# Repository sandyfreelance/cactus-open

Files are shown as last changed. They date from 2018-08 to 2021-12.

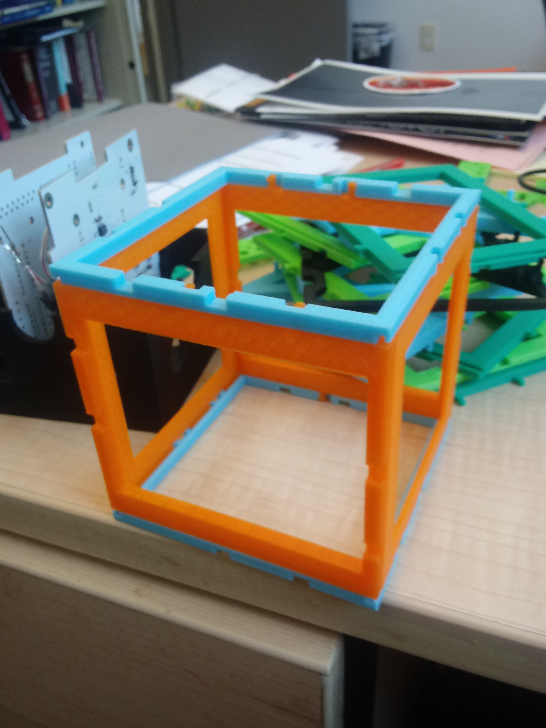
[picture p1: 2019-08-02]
PuzzleSat/PuzzleSat_Pic.jpg

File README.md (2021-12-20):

# cactus-open
Open source documentation, hardware and code for a CubeSat


We provide 4 documents for use by other CubeSat teams, 3 of which comprise our "CubeSat Cookbook".

1) CubeSat_Cookbook_Vol_1_Engineering_Guide.pdf (by R. Pierce Smith) is a comprehensive guide to building your own CubeSat at a detailed engineering level, and includes lessons learned from our Cactus-1 mission.

2) CubeSat_Cookbook_Vol_2_Newcomers_Guide.pdf (by Jorge Rodriguez) is designed for newcomers to CubeSats and discusses some of the overarcing concepts including power, mission readiness reviews, and building effective teams.

3) CubeSat_Cookbook_Vol_3_Common_EPS.pdf (by Erik Schroen) walks you through how to design and customize the electrical power system for your specific CubeSat mission (based on lessons learned from Cactus-1).

4) TheHABHandbook.pdf (by Ian Hastings) is a guide for teams starting up High Altitude Balloon projects.  Under Capitol's "Crawl, Walk, Run" philosophy, we highly recommend teams look at flying payloads and components via HAB as an effective way to iteratively improve your designs.

Acknowledgements: The Cactus-1 mission is Capitol Technology University's first CubeSat mission. Our launch opportunity was provided via the NASA CubeSat Launch Initiative. The Cactus-1 mission is supported by grants from the Maryland Space Grant Consortium (MDSGC).

5) We also provide Ralph Stormer III's "PuzzleSat" 3D-printable CubeSat structure models.  This is a simple modular system for building CubeSat-spec PC104-size-compliant test frames for 1U, 2U, 3U, and other variants so engineering teams can practice working within the CubeSat size requirements.  Documetation, STL and CAD files, and a photo are provided.  They are also fun for prototyping, and we use them for student payload low altitude tests as well.

6) We also provide our hardware schematics, CAD files, and anxillary data to help jumpstart other teams.  Our hardware on this github repository is released under the CERN Open Hardware License version 1.2.  Credit for the Work should be given to R.P. Smith in terms of authorship.  Individual items will indicate citation/credits as well.  Generally, you can use this to build your own CubeSat, the full license terms are below.

* Cactus-1 contains the files for our specific architecture
* CADD Files contains the Cactus-1 stack and board designs used
* EaglePCBs contains PC104, solar, and other bus panels suitable for modding

***********************************************************************

Specific citations and history are given for each component as follows:

Cactus-1 proposals and mission overviews: A. Antunes, R. Schrenk, R. P. Smith, A. Walters, R. Maharaja, M. Horvath

Hermes payload (on Cactus only-- for Hermes sounding rockets, see Maharaja) by C. Murray, E. Schroen (power Board design), Carlos Del Cid, R. Maharaja, P. Smith, IP rights retained by R. Maharaja

Trapsat payload by R. Schrenk, K. Moore, Z. Richards, M. Strittmatter, A. Walters, R. P. Smith, IP rights retained by R. Schrenk

3U++ Tabbed Frame: by R. P. Smith, R. Schrenk, provided under an open hardware license

Pi-CPU/Health & Safety Boards: by R. P. Smith, A. Antunes, provided under an open hardware license

Power bus: by R. P. Smith, G. Auvray, C. Odigwe, A. Antunes, R. Schrenk

Solar: (Added this because power and solar have different aspects (i.e. licensing to use) by R. P. Smith with assembly help from George Gieomekis, Marcus Bailey, Sam Lawson, Nick Keller, Sarah Sharpe, Alex English, Nick Aniello, Chris Finch

Passive Magnetics: by E. Routhier, B Reese , R. P. Smith with help by Ian Hastings, Christina Williams

Flight software by A. Antunes with help by Randy Powell, Zalika Dixon, and thanks to Alan Cudmore for useful discussion on his “PiSat” concept

Thermal blankets by R. Schrenk with help by Sarah Sharpe, Marcus Bailey, and George Giakoumakis

Comms: by M. Horvath, A. Johnson, A. Antunes

Burn wire, foot switches, inhibits, ports, and subsystems not mentioned: considered either part of the above, part of the general Cactus mission, or not sufficiently novel to merit publication or separate enumeration.

Ground team: Mark Horvath, Charis Houston, Devon Marshall, Seth Dickerson

Full list of high-level support (addendum): Alex Antunes, Angela Walters, Rishabh Maharaja, Marcel Mabsen, Patrick Stakem, Alan Cudmore, Dave McComas, Suzanne Strege, Alison Evans, Cinnamon Wright

Full list of students (addendum): Pierce Smith, Ryan Shrenk, Nathan Weideman, Mark Horvath, Alec Johnson, Chris Murray, Sarah Sharpe, George Giakoumakis, Marcus Bailey, Xavier Guzman, Marissa Jagernath, Chukwuma Odigwe, Keegan Moore, Zack Richard, Jamil Ahmed, Gary Visser, Joshua Joseph, Eric Ruthier, Sean Mullin, Christina Williams, Nick Aiello, Randy Powell, Mikus Bormanis, Christel Gesterling, Zalika Dixon, Mike Stritmatter, Josh Hernendez, Ralph Stormer III, Dan Whiteside, Bryce Reese, Charis Houston, Devon Marshall, Seth Dickerson, and others.

uploaded July 2019, updated Dec 2020

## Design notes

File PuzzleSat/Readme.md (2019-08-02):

PuzzleSat
By: Ralph A Stormer III

This work (both document and 3D printable CAD files) are licensed under a Creative Commons Attribution-NonCommercial-ShareAlike 4.0 International License. (https://creativecommons.org/licenses/by-nc-sa/4.0/).  Authorship is Ralph A. Stormer III.

PuzzleSat is a 3d printable modular CubeSat shell and internal structure system. With this system, one can build CubeSat of varying forms and configurations, including 1U CubeSats, 3U × 3U × 3U CubeSats, and miscellaneous formations like rings, spheres, and cacti (a U refers to a standard CubeSat unit which is a decimeter cube (Walker, 2017)).  As of the 7th iteration of the design, the system consists of 13 parts that interlock together to form a shell.  All parts are based off plates that interlock to form the structural support for the PC/104 Printed Circuit Board (PCB) standard. This system is meant for engineering modeling of CubeSats, as to give developers an idea of how the final product would be wired and effectively look.

Common

The common parts are the parts that one would be printed out for every CubeSat size.

Skeletal Female

The skeletal female part is one of the main structural components of PuzzleSat.  It holds the slots for a slide part as well as the openings for the snap fits of the male parts.  The term skeletal refers to there being a bracing structure in between the outer rim of this panel.  This part's secondary purpose is to act as a wall to the outside of the CubeSat.

Skeletal Male

The skeletal male part is one of the main structural components of PuzzleSat.  It holds the slots for a slide part as well as houses the snap fits that integrate with the openings of the female parts.  The term skeletal refers to there being a bracing structure in between the outer rim of this panel.  This part's secondary purpose is to act as a wall to the outside of the CubeSat.

Skeletal Slide

The skeletal slide part is a thin slide that integrates with both male and female parts.  This part allows for the PC/104 board to fit inside of the CubeSat without interfering with the other structural components.  The term skeletal refers to there being a bracing structure in between the outer edge of this panel.  This part's secondary purpose is to act as a wall to the outside of the CubeSat.

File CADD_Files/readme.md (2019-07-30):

Reference files and parts list for our PC104 boards.

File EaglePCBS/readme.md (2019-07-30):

Here are our Cactus-1 solar and bus panels in Eagle CAD format.
Other missions are free to use or repurpose these.readme.md

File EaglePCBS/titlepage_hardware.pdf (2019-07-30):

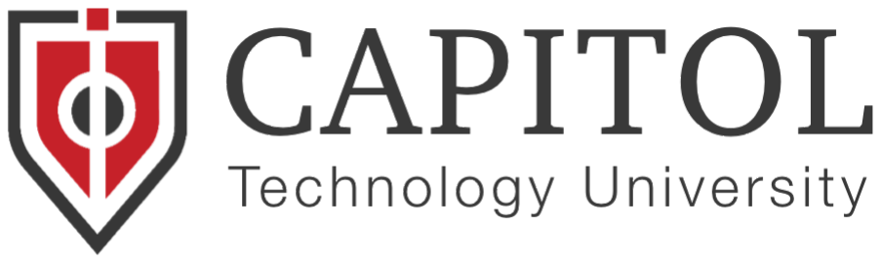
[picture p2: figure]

We provide these documents to support the CubeSat community.

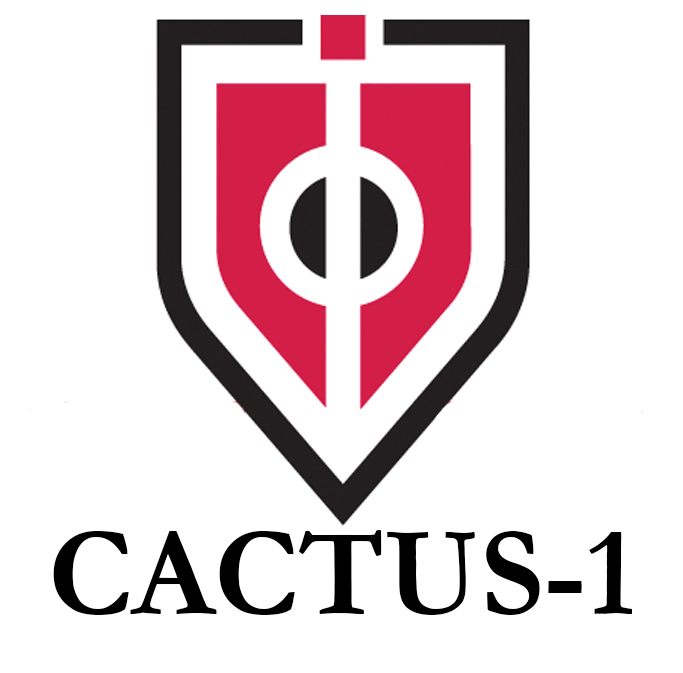
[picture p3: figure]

Acknowledgements: The Cactus-1 mission is Capitol Technology University's first CubeSat mission. Our launch opportunity was provided via the NASA CubeSat Launch Initiative. The Cactus-1 mission is supported by grants from the Maryland Space Grant Consortium (MDSGC).

All hardware is released under the CERN Open Hardware License version 1.2. Credit for the Work should be given to R.P. Smith in terms of authorship. Individual items will indicate citation/credits as well. Generally, you can use this to build your own CubeSat, the full license terms are in the included license file for CERN Open Hardware Licence v1.2.

Specific citations and history are given for each component as follows:
Cactus-1 proposals and mission overviews
A. Antunes, R. Schrenk, R. P. Smith, A. Walters, R. Maharaja, M. Horvath
Hermes payload (on Cactus only-- for Hermes sounding rockets, see Maharaja) by C. Murray, E. Schroen (power Board design), Carlos Del Cid, R. Maharaja, P. Smith, IP rights retained by R. Maharaja
Trapsat payload by R. Schrenk, K. Moore, Z. Richards, M. Strittmatter, A. Walters, R. P. Smith, IP rights retained by R. Schrenk
3U++ Tabbed Frame: by R. P. Smith, R. Schrenk, provided under an open hardware license
Pi-CPU/Health & Safety Boards: by R. P. Smith, A. Antunes, provided under an open hardware license
Power bus: by R. P. Smith, G. Auvray, C. Odigwe, A. Antunes, R. Schrenk
Solar: (Added this because power and solar have different aspects (i.e. licensing to use))
by R. P. Smith with assembly help from George Gieomekis, Marcus Bailey, Sam Lawson, Nick Keller, Sarah Sharpe, Alex English, Nick Aniello, Chris Finch
Passive Magnetics: by E. Routhier, B Reese , R. P. Smith with help by Ian Hastings, Christina Williams
Flight software by A. Antunes with help by Randy Powell, Zalika Dixon, and thanks to Alan Cudmore for useful discussion on his “PiSat” concept
Thermal blankets by R. Schrenk with help by Sarah Sharpe, Marcus Bailey, and George Giakoumakis
Comms: by M. Horvath, A. Johnson, A. Antunes
Burn wire, foot switches, inhibits, ports, and subsystems not mentioned: considered either part of the above, part of the general Cactus mission, or not sufficiently novel to merit publication or separate enumeration.
Full list of high-level support (addendum):
Angela Walters, Rishabh Maharaja, Marcel Mabsen, Patrick Stakem, Alan Cudmore, Dave McComas, Suzanne Strege, Alison Evans, Cinnamon Wright
Full list of students (addendum):
Pierce Smith, Ryan Shrenk, Nathan Weideman, Mark Horvath, Alec Johnson, Chris Murray, Sarah Sharpe, George Giakoumakis, Marcus Bailey, Xavier Guzman, Marissa Jagernath, Chukwuma Odigwe, Keegan Moore, Zack Richard, Jamil Ahmed, Gary Visser, Joshua Joseph, Eric Ruthier, Sean Mullin, Christina Williams, Nick Aiello, Randy Powell, Mikus Bormanis, Christel Gesterling, Zalika Dixon, Mike Stritmatter, Josh Hernendez, Ralph Stormer III, Dan Whiteside, Bryce Reese, and others.

uploaded July 2019

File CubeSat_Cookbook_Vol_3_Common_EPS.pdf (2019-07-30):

The CubeSat Power Bus Design Project is a product by Erik Schroen.

@ 2019 Erik Schroen, all rights reserved

Acknowledgements: The Cactus-1 mission is Capitol Technology University's first CubeSat mission. Our launch opportunity was provided via the NASA CubeSat Launch Initiative. The Cactus-1 mission is supported by grants from the Maryland Space Grant Consortium (MDSGC).

Common Electrical Power System for Small Satellites

Erik Schroen

Capitol Technology University

Dr. Alex Antunes

Department of Astronautical Engineering

AE - 458

Senior Design Project 2

Last Edited by Author: 10 April 2019

Last Edited:

By:

Erik Schroen | EPS

Contents

Acknowledgements

I would like to thank Capitol Technology University for providing connections and support that allows other students and I to participate in high altitude balloon flights, RockSat and other sub orbital flights, and orbital launches. Faculty support has allowed these missions to come to fruition and succeed in accomplishing their goals.
I would also like to thank the RockSat-X, RockSat-XN, and the entire RockSat program and Colorado Space Grant Consortium as well as the supporting members for the great opportunity to fly payloads on their launches. The experience gained from these flights has proven invaluable in the development of this guide as well as providing flight heritage for the designs.
Lastly, I would like to thank the Maryland Space Grant Consortium for their continued support to our university, without which none of these missions would be possible.

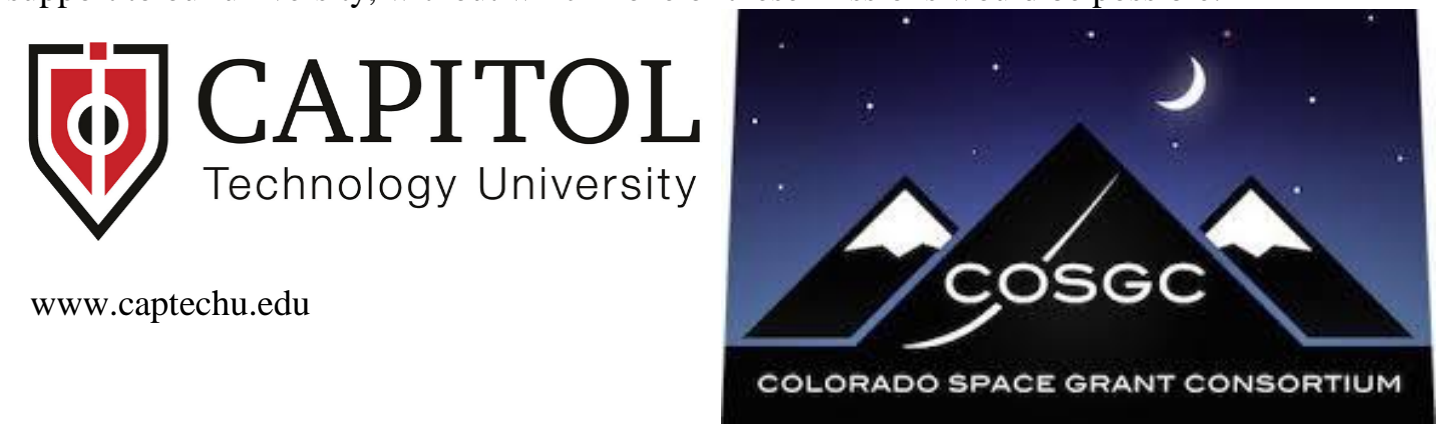
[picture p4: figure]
www.captechu.edu

spacegrant.colorado.edu

md.spacegrant.org

Purpose

The purpose of this document is to discuss a process that an electrical engineer could take to create an Electronic Power System (EPS). This process was determined through my experience gained from multiple orbital, suborbital, and high-altitude balloon (HAB) small satellite missions. The design process will be discussed for each section of the EPS and recommendations will be made. Lessons learned will be provided in relevant sections to discuss any successes, failures, or what could have been done better. The main goal of this document is to speed up the design process of an EPS for a custom small satellite, which is usually the last subsystem to be designed due to changing electrical requirements by other subsystems. This will allow for more testing of the EPS separately and when integrated with the satellite. This documentation assumes a novice level of understanding in electronics, that is at least a circuit theory or equivalent course, an electronic devices course will aid the reader as well.

Biography

I am an Astronautical Engineering major (Graduating May 2019) at Capitol Technology University (CapTechU). At the time of writing this I have flown two successful EPS (Project Hermes 3.0 & Project Aether) and have one EPS waiting for flight that was tested successfully (CACTUS – Hermes) as well as one successful High-Altitude Balloon (HAB) flight for Project Aether. All these projects will be discussed when applicable to apply lessons learned to my designs and techniques. I have worked at U.S. Army Research Laboratory (ARL) for three years in the Sensors and Electron Devices Directorate (SEDD), Power Conditioning Branch, designing (electrically & mechanically), building, and testing/evaluating power systems for multiple purposes.

If you have any questions or need clarifications I can be reached at eschroen2@gmail.com.

Figure 1 - Sections of an EPS discussed in this document; Power Input, Input Power Conditioning, Energy Storage, and Payload Power Conversion

Power Budget

The first thing that should be accomplished is developing a rough power budget for the payload. This can be updated later as systems become more solidified and numbers become more concrete, but you need a basic idea of how much power each system is going to require before you can really get started. This information will determine almost everything hereafter. This initial document should consider the worst-case scenarios, it is always easier to overdesign early and lower the requirements later then to have to increase your requirements after a preliminary design. The most common systems you will have to consider for a university mission are your computer/processing (typ. Raspberry Pi or Arduino), scientific/engineering payload, and communications, though others may apply depending on the specifics of the mission. You should attempt to gather as many datasheets as possible for each component that is likely to fly to help you generate worst case scenarios for each system.

Table 1 - Early power budget for Project Aether

Component | Quantity | Maximum Current (A) | Nominal Voltage (V) | Power (W) | Total Current (A) | Total Power (W)
Raspberry Pi 3 | 1 | 1.3 | 5 | 6.5 | 1.3 | 6.5
Iridium Modem | 2 | 1.3 | 5 | 6.5 | 2.6 | 13
Amplifier | 2 | 0.001 | 7.2 | 0.01 | 0.003 | 0.02
Spectral Camera | 1 | 0.25 | 5 | 1.25 | 0.25 | 1.25
VIPE Transformer | 1 | 3 | 7.2 | 21.6 | 3 | 21.6

Voltage and Current: Table 1 shows the power budget used for Project Aether. Early on the team knew these components would be flying, all the information for maximum current and nominal voltage were taken from datasheets for the devices. The amplifiers and VIPE Transformer could run directly from the batteries so the nominal voltage was the value of the nominal voltage for the batteries, discussed later. The maximum current that each system will draw is important because the components that are selected for the power board must be able to handle the required currents. The other systems would need regulation to achieve 5 V.

Power: Power was a simple calculation from current and voltage (P = I ∗ V). Total current and total power are there to account for the quantity of each device. The total current for all devices can be calculated (7.153 A) and the total power can be calculated (42.37 W) to aid with battery selection later. If the flight time of the payload for suborbital missions or HAB flights or the desired-on time for orbital missions is known, then the Amp-hour (Ah) required can also be calculated to aid in battery selection by Aℎ = t ∗ I where t is in hours. Project Aether was a suborbital sounding rocket mission with a flight time of 15 minutes, so the battery capacity required was 1.79 Ah. Note, this is an estimate because the current draw of the devices may not be the same as the current draw from the batteries.

Energy Storage

After the power budget you can select the batteries that will be flown. The most common battery type and the one that will be used throughout this document is a Lithium-Ion 18650 rechargeable cell. Lithium-polymer cells may also be flown and should be interchangeable in this design so long as the cell voltages are not too low or high. Whichever chemistry is chosen, this should be communicated in your design reviews so it is clear that you are flying batteries and will need time and access to charge them during testing and preflight.

Cell Chemistry: An 18650 cell’s nominal voltage is 3.7 V and the peak voltage at a full charge is 4.2 V. The nominal voltage is where most of the battery’s capacity is, so as the battery discharges it will stay at this voltage for longer, shown in Figure 2. The capacity axis can be taken as discharge over time. With a load applied the battery voltage strarts droping until the nominal voltage, where is very slowly decreases until reaching a point where the voltage quicly drops. At the knee point where the battery voltage drops off the battery is fully discharged. The different curves are different discharge currents, 1C being the lowest and 18C being the highest.

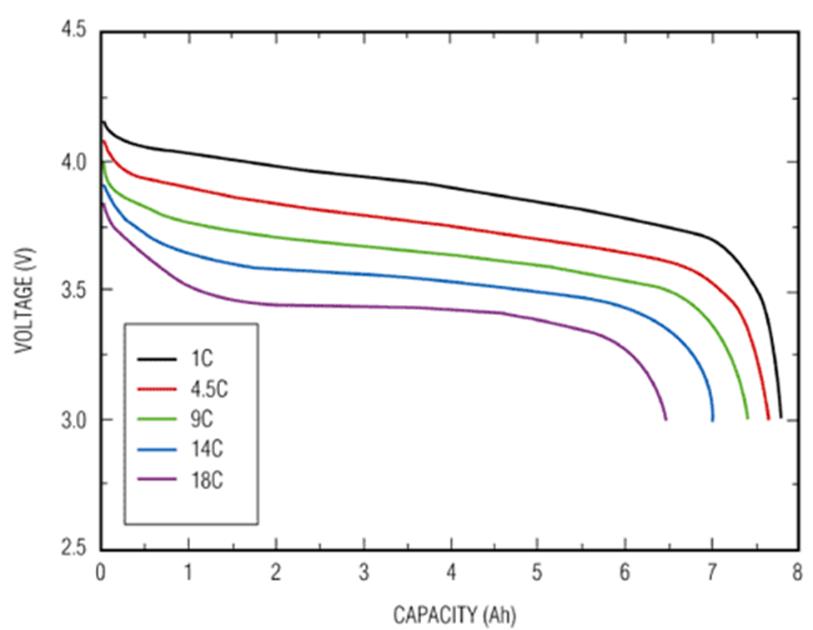
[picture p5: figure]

Figure 2 – Lithium-Ion 18650 battery voltage vs. capacity - Electrical Engineering Stack Exchange

Maintenance: The main thing to be careful of is to not over charge or over discharge the cells, these will destroy them and render them inoperable. Generally, the charger will not allow the cells to be overcharged. However, the cells can be charged directly from a power supply or a custom charger (Appendix), in this case the voltage setpoint should be the peak voltage of the cell and the current should be limited to 1 A maximum or lower. Peak voltages are listed in Table 2. The batteries should be left on the power supply until the current flowing into them is close to zero at the voltage setpoint. Initially when the battery is put on the power supply the battery voltage will ‘float’ up, and once disconnected will also ‘float’ down, therefore the current flow into the battery is the best indicator of state of charge. Over discharge is accomplished by monitoring the battery or cutoff circuitry, when the cell voltage gets too low the battery should be fully charged before continuing use. During charging batteries should never be left alone and should constantly be monitored. As shown in Figure 2, 18650 cells should not be discharged lower than 3 V.

Battery Selection

Creating a Pack: By placing multiple battery cells in series, you create a ‘pack’ with a higher voltage, shown in Table 2 and Figure 3. If multiple cells are used the positive terminal of a battery should always be connected to the negative terminal of another. There will be an overall positive and overall negative terminal which are the power connections to the circuit.

Table 2 – 1 - 4 Lithium-Ion cell battery pack voltages

Number of Cells | Minimum Voltage (V) | Nominal Voltage (V) | Peak Voltage (V)
1 | 3 | 3.7 | 4.2
2 | 6 | 7.4 | 8.4
3 | 9 | 11.1 | 12.6
4 | 12 | 14.8 | 16.8

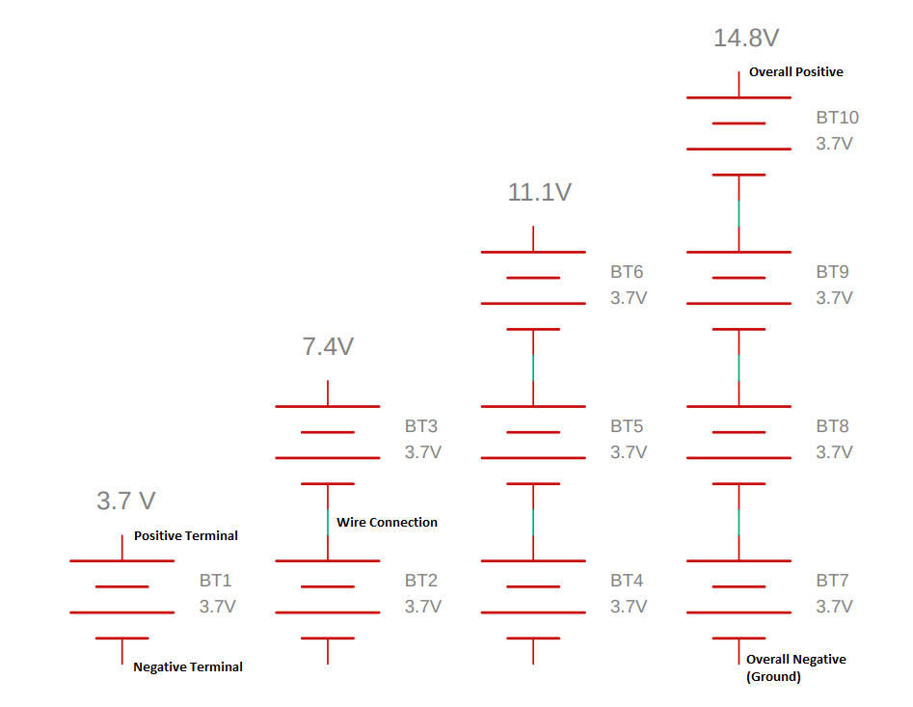
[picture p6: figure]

Figure 3 – 1 - 4 Lithium-Ion 18650 cell battery pack configuration

Voltage: The number of battery cells that you use for a mission comes down to the volume and mass constraints of the EPS and satellite as well as the needed capacity of the EPS, discussed next. A good rule of thumb is to keep the nominal voltage of the battery pack close to the voltage that requires the most current, favoring a slightly higher voltage over a lower voltage. As an example, if the payload has many 5 V devices drawing current, 2 cells in series may be a good choice for the payload.

Current and Capacity: Current and capacity is the next consideration. The maximum possible current draw and required capacity should be obtained from the power budget. Battery cells have a maximum discharge rate, and while adding cells in series increases the batter pack voltage, it does not increase the maximum current discharge rate of the pack. To do this packs must be added in parallel such as in Figure 4. This will not increase the pack voltage but will increase the total capacity and maximum discharge current. Typically, the maximum discharge rate is around 5 - 10 A for 18650 cells, however exact number can be obtained from the data sheets of the cells once they are chosen/purchased. The typical capacity is around 1,500 – 3,600 mAh depending on the quality of the cell. The total number of cells in the packs determines the capacity, so in the case of Figure 4 there are 4 cells total, if each has a capacity of 2,000 mAh that gives the pack a total capacity of 8,000 mAh or 8 Ah. Meanwhile the maximum discharge current will be determined by the number of parallel branches, in the case of Figure 4 there are 2 branches, if each cell has a maximum discharge current of 5 A, that will give the pack a maximum discharge current of 10 A. Any number of branches can be added to meet the design requirements of the EPS, however, keep volume in consideration when selecting the number of cells. Common dimensions for 18650 cells are given in Figure 5 for planning.

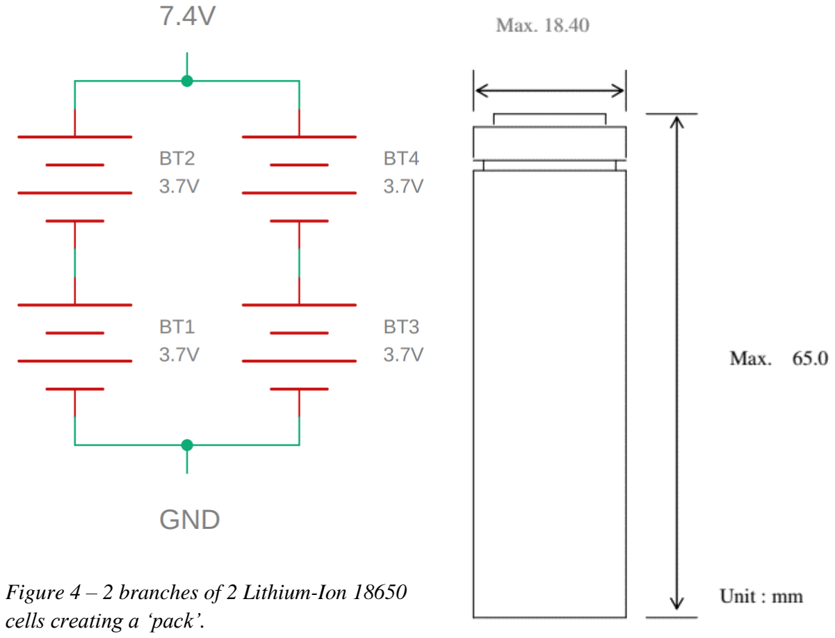
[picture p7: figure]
cells creating a ‘pack’.

Figure 4 – 2 branches of 2 Lithium-Ion 18650

Figure 5 – Common Lithium-Ion 18650 cell dimensions – batteryspace.com

Purchasing: I have bought 18650 cells from Amazon, DigiKey, and BatterySpace and have had no issues with the cells I received. When looking for cells you must be cautious of outrageous claims on capacity level. Some will claim capacities of 5,000 mAh which is impossible with our current technology. The following are cells I have found:

- Amazon (www.amazon.com): Search for 18650 Lithium Batteries, I have used EBL, but any with reasonable claims and good review should suffice, currently $3.25 per cell ($12.99 4 pack)
- DigiKey (www.digikey.com): Search 18650 and select Batteries Rechargeable (Secondary), there will be a few options, you most likely want to use a single cell, (3.6 or 3.7 V voltage rated). SparkFun Electronics has single cells for $5.95.

- BatterySpace (www.batteryspace.com): Select Lithium Ion Batteries, Li-Ion/Polymer Single Cells, 3.6V/3.7V Li-Ion Cylindrical Cell Series, 18650/20700/21700 Rechargeable Batteries, large selection of 18650 cells, $5.15 - $13.95 (Ensure they are 18650 cells, there are other cell types listed), choice can be made based on capacity and price considerations.

For chargers most will be for single cell chargers, so once the battery pack is made it will not be able to be charged from a single cell charger without disassembly. Instead, charge from a power supply which was discussed in the Maintenance section. I have found the following chargers:

- Amazon: These are tricky to find, searching for 18650 chargers will result in many single cell chargers (EBL has packs that come with these, great if you need cells as well). Tenergy TLP-2000 is a fantastic charger and I highly recommend this, it can select charge from 1 – 4 Lithium cells and has alligator clips which can be directly connected to the overall positive and negative terminals of the pack.
- DigiKey: Search 18650, Click Battery Chargers, not many and they are single cell chargers.
- BatterySpace: Some single cell chargers in the same place the cells were located.

Electrical Input

RockSat

For a RockSat mission, you will want to tell the reviewers that you require a input pulse from the rocket, most of the time for my missions this was at T – 0 (launch), but this pulse could be whenever during the launch you prefer your payload to activate (stage separation, second stage ignition, skirt separation, etc. or any specific time interval). Keep in mind the time it will take for the payload to initialize (Pi/Arduino boot time, etc.). This input pulse will be a 28 V pulse, with a selectable duration (1 second was used for my payloads and was more than enough). Figure 6 shows a circuit which was flown multiple times with constant success, each part will be evaluated after the image. The part numbers I used are listed and can be rebought and used again for any mission using 1 – 4 18650 cells, however, new, improved, and cheaper parts are always surfacing, I will explain what is required to select your own parts as well.

Figure 6 - Electrical input used for RockSat launches, successful on Hermes 3.0, Aether, and HAB flights.

Component Breakdown: This circuit takes an input from the rocket timer event line, protects against unexpected transients, creates a constant current source from the signal to turn on an optoisolator, which isolates the onboard battery power from the rocket’s power system. The optoisolator then activates an SCR which turns on a MOSFET to allow the battery power to begin flowing into the system. Each part’s role in the design is described below and the process for which I selected them is outlined.

- Timer Event Launch & Rocket GND –These connections are to the connector to the rocket. These should just be through hole connections that wires (typ. 18 or 20 gauge) can be soldered into to make a connection with the external connector to the rocket. This is not the 28 V rocket power connection, it is the timer event pin which should only enable for a limited amount of time after launch or whenever you decide to activate your payload, the other connection is to the rocket’s ground.
- D1 – This is a protection diode which prevents a reverse current (either transient or from incorrect polarity) from destroying the circuit. Search for diode on DigiKey and select Diodes – Rectifiers – Single then use the following filters:
- Packaging: Cut Tape (CT)
- Part Status: Active
- Stock Status: In Stock
- Mounting Type: Surface Mount
- Voltage – DC Reverse (Vr) (Max): This is the voltage that the diode can hold off if applied in the reverse direction, this must be equal to or greater than 28 V, 35 V or greater will provide plenty of headroom.
- Current – Average Rectified (Io): This is the average forward current the diode can conduct constantly without damage, this needs to be equal to or greater than the output of the constant current source U1 (20 mA in this case), overhead is good as always.
- At this point you could sort by ascending unit price and these parts should work for you, however for ease of soldering I would suggest the following filter (The part I used is an SMA, extremely small package and difficult to solder, lesson learned):
- Supplier Device Package: SMB & SMC
- These parts will be large enough to easily solder, just check to make sure the parameters all work for your conditions and the operating temperature is within range for mission/space setting, and again sort by unit price ascending.

- D2 – This is a transient voltage protector, protecting from overvoltages to the system, this will clamp the voltage applied to the system to the breakdown voltage of the diode. Search for diode on DigiKey and select TVS - Diodes then use the following filters:
- Packaging: Cut Tape (CT)
- Part Status: Active
- Stock Status: In Stock
- Mounting Type: Surface Mount
- Voltage – Breakdown (Min): This is the minimum voltage the diode will break down and begin to clamp at, so this needs to be higher than the input pulse voltage (28 V) but lower than the U1 maximum allowed voltage (38 V for the example U1). 30 V – 35 V is a good starting range (33.3 V for the example D2).
- At this point you could sort by ascending unit price and these parts should work for you, however for ease of soldering I would suggest the following filter:
- Supplier Device Package: SMB & SMC
- These parts will be large enough to easily solder, just check to make sure the parameters all work for your conditions and the operating temperature is within range for mission/space setting, and again sort by unit price ascending.
- Note: Some of the parts are unidirectional and some are bidirectional, both will work perfectly fine. Bidirectional is essentially two diodes in opposite directions back to back and will clamp in both directions, while unidirectional is only a single diode. With bidirectional the orientation will not matter when soldering, with unidirectional you must ensure that the cathode is on the positive rail and the anode is on the negative rail/ground such as in the example circuit.

- U1 – This is a linear regulator which typically provides a fixed output voltage so long as the input voltage is a certain voltage above it (typ. 1.25 V), however this one is set up in a constant current supply configuration. This provides a constant current that is safe and guaranteed to turn the optoisolator on. Search for Linear Regulator on DigiKey and select PMIC – Voltage Regulators - Linear then use the following filters:
- Packaging: Bulk, Cut Tape (CT), and Tube
- Part Status: Active
- Stock Status: In Stock
- Mounting Type: Surface Mount
- Output Configuration: Positive
- Output Type: Adjustable
- Number of Regulators: 1
- Voltage – Input (Max): This must be equal to or greater than 28 V, 35 V will provide plenty of headroom (38 V for the example U1).
- Current – Output: This must be equal to or greater then what’s required to turn the optoisolator on (typ. ~20 mA, and ~50 mA is typically their max). Greater than or 50 mA will provide headroom.
- Sort by price ascending and check the operating temperature is within acceptable range. Anything with LM317 will work great, I would suggest not going with a complicated package (such as 8-SOIC) as only 3 pins are required for this part, a DPAK or SOT-223 will work great.

- R1 – This resistor sets the output current of the constant current regulator, there will be a formula for this in the linear regulator datasheet under a section labeled Current Limiter or Current Regulator, which is typically I =

1.25 V
R1

, check the part datasheet to confirm this. So, if ~20 mA is needed to turn the optoisolator on a 62.5-Ω resistor is needed. Next you need to find the power that the resistor will use, which can be found using P = I

2
∗
R, this will be used to select the package, the power for the 20-mA case is 25 mW. Search for resistor on DigiKey and select Chip Resistor – Surface Mount then use the following filters:
- Packaging: Cut Tape (CT)
- Part Status: Active
- Stock Status: In Stock
- Resistance: Use a 1% standard resistor value chart, Figure 7, and select the closest 1% value resistor to the needed value (I would recommend going with the next lower value, so the linear regulator creates slightly more current). In the 20-mA case I would select 61.9 Ω.
- Supplier Device Package: From this point I would limit the package, 0805 is the most common package and relatively easy to solder, this is the smallest I would go. Power needs to be taken into consideration, each common package has a maximum power of:
- 0805: 125 mW
- 1206: 250 mW
- Sort by price ascending and check the operating temperature is within acceptable range.

- C1 & C2 – These are suggested capacitors for stable operation of the linear regulator which can be found in the linear regulator datasheet under the Typical Application section. 100 nF is typical for the input capacitor to most Integrated Circuits (IC), and 1 µF is typical for the output of a LM317, however this may change depending on the chosen chip. Search for capacitor on DigiKey and select Ceramic Capacitors then use the following filters:
- Packaging: Cut Tape (CT)
- Part Status: Active
- Stock Status: In Stock
- Capacitance: Select the required capacitance value as described in the datasheet.
- Voltage – Rated: This needs to be equal to or greater than 28 V, headroom is always good (typ. 50 V).
- Temperature Coefficient: X7R, this is a rating of how much the capacitance value will change with temperature, X7R is one of the best and I would recommend selecting this.
- Mounting Type: Surface Mount, MLCC
- Package/Case: I would recommend 0805 or 1206
- Sort by price ascending and check the operating temperature is within acceptable range.

- U2 – This is the optoisolator or optocoupler, this device electrically isolates the rocket from your payload through an optical medium. When current is applied to the LED on the left side in the diagram, it activates a phototransistor on the right side of the diagram which then allows current to flow through it, with no light, no current flows (except for a very small leakage current). Search for optoisolator on DigiKey and select Optoisolator – Transistor, Photovoltaic Output then use the following filters:
- Packaging: Cut Tape (CT)
- Part Status: Active
- Stock Status: In Stock
- Mounting Type: Surface Mount
- Number of Channels: 1
- Output Type: Transistor
- Current – Output/Channel: This value must be large enough to turn D3 on, which is typically quite low, I would still suggest selecting greater than or 30 mA at least.
- Sort by price ascending and check the operating temperature is within acceptable range. There will be a chart in the datasheet that will have Collector Current vs. Collector-Emitter Voltage with different Forward Currents (IF). This chart is used to determine the forward current you need. For the part chosen in my design you can see a 20 mA forward current provides enough collector current at around 7.2 V (your nominal battery pack voltage) of Collector-Emitter Voltage (~18 mA) to activate D3. Selecting a target forward current will then allow you to select U1 and R1, just ensure the selected value is within safe operating conditions located in the Electrical Characteristics chart.
- R2 – This is a current limiting resistor to protect D3. The value depends on the SCR (D3) chosen but allowing around 5 mA of current should work for most. Use the nominal battery voltage from your battery pack to select this value and the gate voltage drop of D3 (800 mV for an estimate), R =

Vnominal−VSCR
I

. The 1.1 kΩ in the diagram permits 8 mA of

current. Follow the R1 guide and select the required 1% value resistance for this case.

- D3 – This is an SCR which, once activated through a gate signal (current through R2) will allow current flow through it so long as it is above a certain holding current. When it falls below this value it will no longer conduct and will require another gate pulse to activate. We will use this to disconnect the batteries from our payload normally until activated by the rocket, then the batteries will supply power to the payload until the battery voltage falls too low. Search for SCR on DigiKey and select Thyristor - SCRs then use the following filters:
- Packaging: Cut Tape (CT)
- Part Status: Active
- Stock Status: In Stock
- Mounting Type: Surface Mount
- Voltage – Off State: Ensure these values are greater than the maximum battery voltage (8.4 V in the example case).
- To limit the remaining parts down will take some trial and error. Ideally you want to select the lowest Current – Hold (Ih) (Max) for the least amount of waste power, however you need to ensure the Voltage – Gate Trigger (Vgt) (Max) and Current – Gate Trigger (Igt) (Max) are sufficiently low that U2 can supply the necessary current with the selected forward current, and the battery nominal voltage. I would recommend using the example part as a guide at the very least to compare values.
- Sort by price ascending and check the operating temperature is within acceptable range, also paying attention to the package type and size for solderability and size considerations on the Printed Circuit Board (PCB).
- R3 – This resistor will set up the holding current for the SCR. To calculate this value, take the Current – Hold (Ih) (Max) of the selected SCR, the Voltage - On State (Vtm) (Max) of the SCR, and the minimum voltage of the battery pack which is 6 V in the example circuit. Then calculate R =

Vmin−VF
IH

, where Vmin is the minimum voltage of the

battery pack, VF is the on state voltage of the SCR, and IH is the holding current of the SCR. This gives us 860 Ω or 866 Ω for a standard 1% value. Follow the R1 guide and select the required 1% value resistance for this case.
- J3 – This is an inhibit connector which is just 2 through holes to solder wire into on the PCB. The wires should be connected to a locking switch or a jumper that is accessible to a user on the outside of the payload. This inhibit ensures the system does not activate inadvertently and allows the payload to be switched off if switched on during testing.

- J2 – This should be an accessible connector to the outside of the payload which connects to the battery overall positive and negative for charging. This connector should be covered when not in use to prevent accidental short circuits.
- A protection diode could also be added to prevent a reverse charging current to be applied (this would destroy the batteries and/or charger) which would be added on the positive line with the anode facing the port. With this in the forward drop of the protection diode must be accounted for when charging (charging voltage will be the maximum voltage of the battery pack plus the forward drop). This can be minimized by using a low drop Schottky diode which can be found on DigiKey by searching for Diode and then selecting Diodes – Rectifiers – Single and following the same selection process as D1. The Voltage - DC Reverse (Vr) (Max) must be greater than your maximum battery pack voltage and the Current -Average Rectified (Io) must be greater than your charging current.
- The alternative to this is ensuring the charging connector is a one-way connector, that is, it cannot be plugged in backwards (we used a Dean Connector for this).

- M1 – This is the p-type MOSFET which functions as an electronic switch. This blocks the battery voltage from the payload until the activation signal is received, where it then connects the battery voltage to the payload and converters. When the voltage on the gate is equal or close to the voltage on the source, the MOSFET is closed, no current flows. When the voltage on the gate is much lower than the voltage on the source the MOSFET is open, current flows relatively unimpeded (small on-state resistance). Search for MOSFET on DigiKey and select Transistor – FETs, MOSFETs - Single then use the following filters:
- Packaging: Cut Tape (CT)
- Part Status: Active
- Stock Status: In Stock
- FET Type: P-Channel
- Mounting Type: Surface Mount
- Drive Voltage (Max Rds On, Min Rds On): This device needs to be ‘Logic Level’ since the forward drop of D3 will apply a voltage on the gate when we need the MOSFET to be on. Selecting 4.5V, 10V will give a large selection of Logic Level devices that will work in this application.
- Drain to Source Voltage (Vdss): This must be greater than or equal to the maximum battery voltage, with overhead.
- Current – Continuous Drain: This must be greater than the maximum current determined in the worst case for your power budget. In the example case 25 A was selected.
- Vgs (Max): This value must be equal to or greater than the maximum battery pack voltage, again with overhead.
- The parts can now be sorted by price ascending.
- The lower the value of Rds On (Max) @ Id, Vgs the better, this is the resistance of the device when it is on, higher values lead to excess heat generation and inefficiencies.
- For the package, D-PAK, TO – 252, and D

2
-PAK will work fine.
- Ensure operating temperature is within range
- D4 – This is a protection diode for the MOSFET. When the inhibit is pulled and the MOSFET is conducting current and attempts to turn off, the inductance in the PCB traces can slam the MOSFET with a high voltage spike, this diode clamps this voltage spike below the Drain to Source Voltage (Vdss) to protect the diode. The process for selecting this is the same as D2, however the Voltage – Breakdown (Min) should be less than the Drain to Source Voltage (Vdss) of the MOSFET but greater than the maximum battery voltage, for the example I selected 22.2 V while the Drain to Source Voltage (Vdss) was 30 V and the maximum battery voltage was 8.4 V.

This concludes the design breakdown for the example, this circuit can be used by any payload with 1 – 4 18650 cells so long as the current required by the payloads is within range of M1. The number of batteries in series will determine R2 and R3, all other parts are usable with any amount of batteries so long as current limits are not exceeded for your payload.

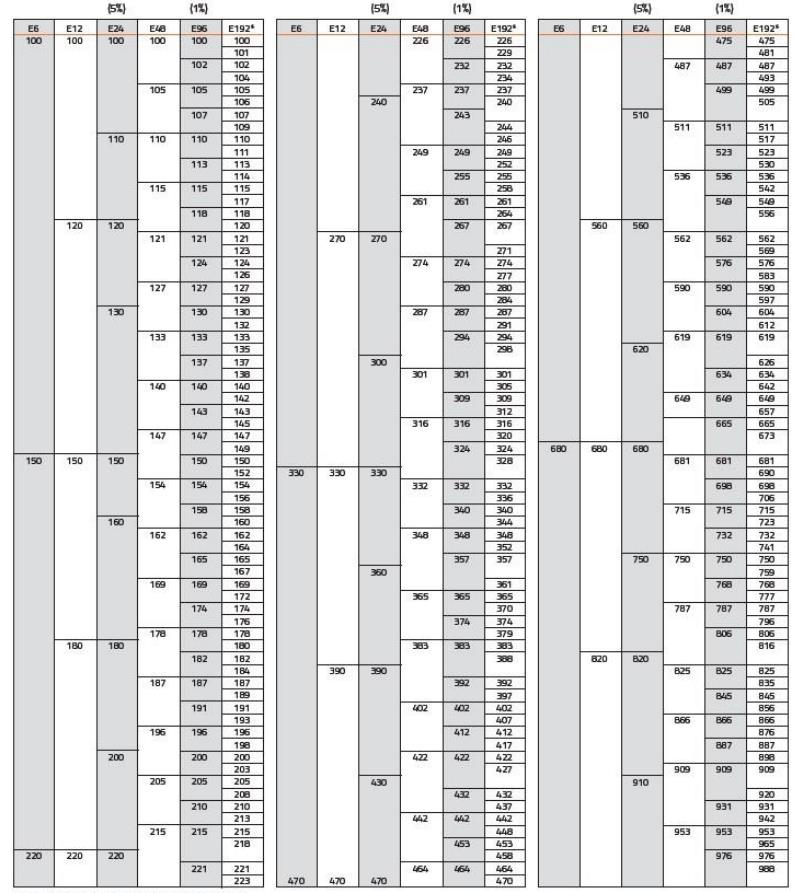
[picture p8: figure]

Figure 7 - Standard resistor values (Use the 1% column). When using calculations, it is inevitable the exact resistance value will be a common value. This chart lists the common resistance values that are manufactured. 1% resistors are common and cheap with good resistance resolution. Using this you can select the closest resistor value to what was calculated (multiply or divide by 10 as much as needed, e.g. 182 is 182 Ω, 18.2 Ω, 1.82 kΩ, etc.). – Venkel

CubeSat/Small Satellite

Solar Panels

Solar Panel Basics: Solar panels are Photovoltaic (PV) junctions which convert light into energy. Solar panels primarily function as current sources up to a certain voltage. Figure 8 shows the typical shape of a Current vs. Voltage curve for a solar panel. The power output of the cell will be the area of a rectangle under the curve with on corner on the origin and the other at some point on the curve. The maximum power will be produced at some point on the knee (2.33 V and 14.6 mA for this curve, producing 34 mW) which is the ideal operating point. Two other useful numbers are the Open Circuit Voltage, which is the highest voltage the cell can produce under no load and under full illumination (2.62 V for the example cell) and the Short Circuit Current, which is the maximum current produced when the cell is shorted and under full illumination.

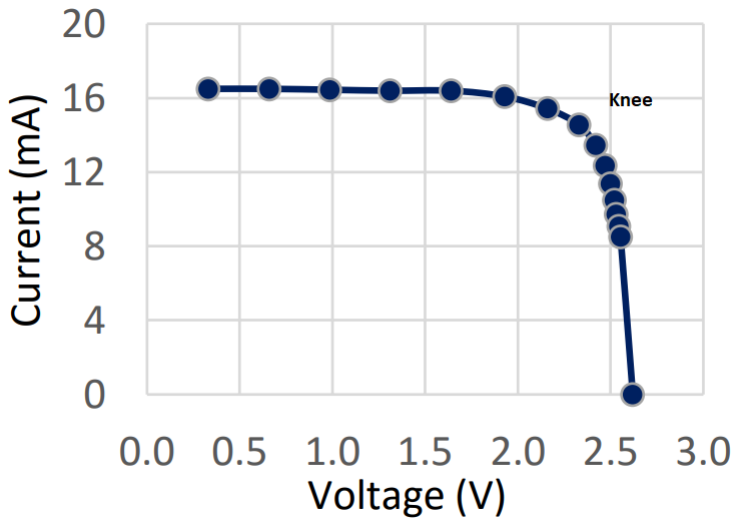
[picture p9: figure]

Figure 8 - TrisolX Solar Wing I-V curve - TrisolX

Solar panels were used on the CACTUS – Hermes 3.0 payload, however the panels were supplied to us by the CACTUS team. Solar panel discussion on the panels that were used can be found in the document by Smith, R. P. found in the Reference/Additional Reading section. Here I will discuss what you should consider when selecting solar panels for your mission and summarize lessons learned from the CACTUS team.

Solar Panel Consideration: There are two main considerations when deciding on what solar panel to use for your mission, these are the efficiency of the cell and the packing efficiency of the cells. With a very limited amount of surface area on small satellites power is a huge problem because of the limited amount of solar panel coverage possible. CACTUS – Hermes 3.0 ran into the issue where our input power was so low that our Raspberry Pi in sleep mode would drain more power then was generated by the solar panels. The greater power conversion efficiency the more power that can be extracted from the solar panel area. The solar panels used were TrisolX Solar Wings which are triple junction Gallium Arsenide solar cell with 28% efficiency, shown in Figure 9. 28% efficiency is quite high when talking about solar panels, and triple junction will typically be the typical panel used for any space application because of their much higher efficiency, however, they are fragile so handle with care.

However, packing efficiency is also a large concern, this is defined as the amount of wasted area (non-solar panel) on the solar panel board. Figure 9 shows the shape of the solar panels that were used on the CACTUS payload, and Figure 10 shows the design of the solar panel PCB. While these panel may be high efficiency, you can see their odd shape. This odd shape led to a lower packing efficiency then was possible with rectangular cells of the same efficiency. Space is needed between the panels for solderability and to prevent short circuiting of the panels, however, it is evident if the solar panels were rectangular, the packing efficiency could have been much higher, increasing the solar panel area on the board, and increasing the total power of the board, under the assumption that the rectangular solar panels were the same efficiency. Because of packing efficiency, it may be advantageous to select a lower efficiency panel if it increases the packing efficiency enough to offset the loss.

Figure 9 - TrisolX Solar Wing panel - TrisolX

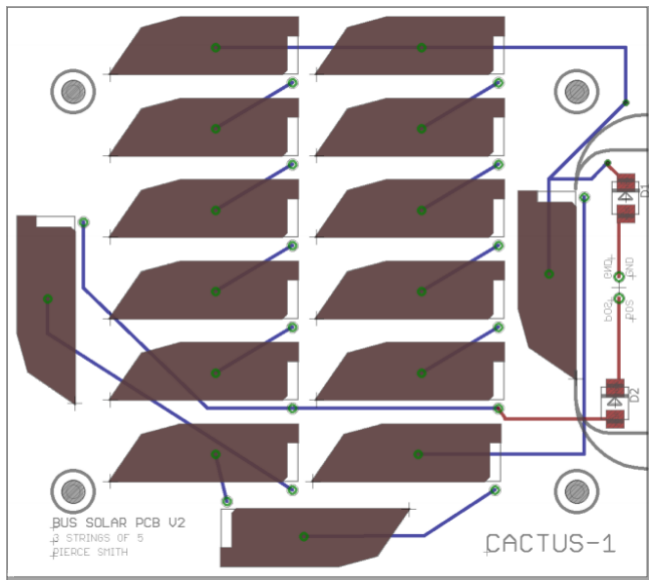
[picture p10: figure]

Figure 10 - CACTUS Solar Panel PCB Layout - Smith, R. P.

Solar Panel Selection: It is recommended that you select multiple different options for solar panels and create a PCB layout to determine the maximum packing efficiency possible. Remember some keep out space must be kept between the panels to allow them to be properly soldered in and to prevent electrical faults. From this design you can calculate the maximum power output of the board. From there you can select the board with the most power while also considering the total cost of the solar panels (Another reason the TrisolX panels were picked were their high efficiency and low cost). Always ensure the operating temperature is within limits.

There is some selection of solar panels on DigiKey, you can find them by searching Solar Cell and selecting Solar Cell then select the following filters:

- Part Status: Active
- Stock Status: In Stock
- From here you can browse the selection, paying attention to the size of the cell mainly (this can be restricted in the filters if desired) and the voltage the cell produces. I would recommend looking at the image/datasheet of the cell to determine whether the cell comes with wire leads or a solderable tab, while both can be used, the solderable tab will permit a higher packing efficiency.

This is not the only place to find panels however, many independent companies sell panels (such as TrisolX) and research must be done to find a panel which best suits your mission in terms of size, price, and efficiency.

Voltage: Just like batteries, solar cells can be connected in series to increase the voltage of the string, with the positive terminal of one cell connected to the negative of another cell and one overall negative and positive connection for the string, shown in Figure 11. Strings of the same voltage can then be connected in parallel with each other to increase current. A diode should always be connected on the overall positive of each string. This is because when a cell or string is not within sunlight, they can turn into current sinks, absorbing all or most of the current produced by the other cells.

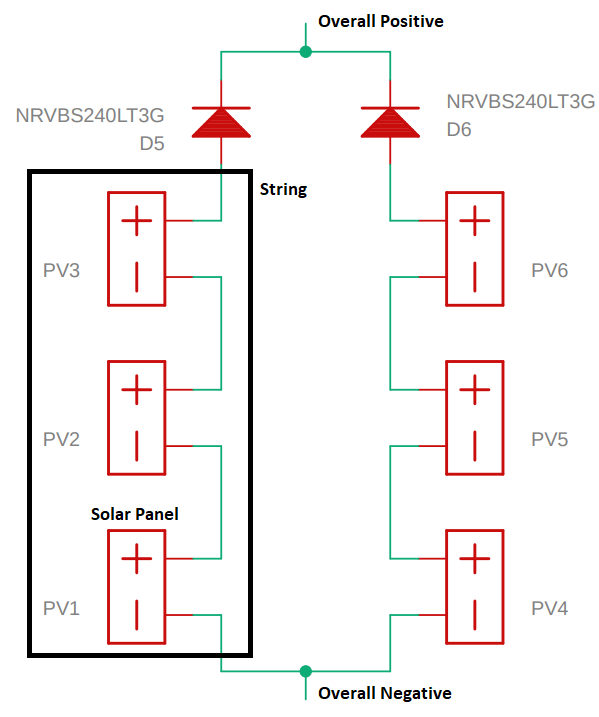
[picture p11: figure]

Figure 11 - Solar panel string configuration

Part Selection: This circuit provides electrical connections for power input into a system from any number of solar cell strings.

D5 & D6: These diodes protect from current sinks as described previously. These ideally should be low forward drop Schottky diodes to reduce losses. To find these search Diodes on DigiKey and select Diodes – Rectifiers – Single then select the following filters:

- Stock Status: In Stock
- Packaging: Cut Tape (CT)
- Part Status: Active
- Diode Type: Schottky
- Mounting Type: Surface Mount
- Supplier Device Package: Again, I would recommend an SMB or SMC for solderability, but this is not necessary
- Voltage – DC Reverse (Vr) (Max): This value must be equal to or greater than the total sum of the open circuit voltages of the solar panels in the string. If each cell has a 2.5 V open voltage in Figure 21, then this value must be equal to or greater than 7.5 V, headroom is encouraged (40 V for the example).
- Current - Average Rectified (Io): This value should be higher than the short circuit current of the panels in the string. Notice this is not the sum of all the panels, just the maximum of one panel because that also sets the maximum current of the string. If the short circuit current of the panels in Figure 11 is 20 mA, then the value must be equal to or greater than 20 mA
- At this point a selection can be made, I would recommend sorting by Voltage - Forward (Vf) (Max) @ If Ascending to select the lowest possible value in this column, keeping price in mind. Doing this will minimize efficiency losses for the strings.
- Ensure the operating temperature is within limits.

Input Conditioning

At this point the voltage output of the solar panels needs some way of interfacing with the batteries, there are 3 ways to do this.

DC/DC Converter: This is the most efficient and recommended way to interface the solar panels with your energy storage. This will convert the voltage created by the solar panels into a voltage usable by the batteries with minimal waste. The downside of this circuit is that it is more complex and has more components then the other circuits. With this circuit the solar panel string should have a maximum open circuit voltage that is lower than battery voltage to ensure the converter is always operating in an efficient manner. Figure 12 shows the example circuit.

Figure 12 – DC/DC converter interface between a solar input and energy storage

Component Breakdown: This circuit takes the solar panel input voltage and converts it into a charge voltage for the batteries.

- U3: This is the main converter chip which will produce the correct output voltage. The datasheet for this part will also have all the other parts needed for the circuit as well as equations to calculate their values. To find these parts search DCDC on DigiKey and select PMIC - Voltage Regulators - DC DC Switching Regulators. From there refine the search with the following filters:
- Packaging: Cut Tape (CT), and Tube
- Part Status: Active
- Function: Step Up
- Output Configuration: Positive
- Topology: Any selection containing Boost (not slashed with another word, only ones separated by commas)
- Output Type: Adjustable
- Number of Outputs: 1
- Mounting Type: Surface Mount
- Stock Status: In Stock
- From here you can sort by price ascending and begin searching, the following things must be kept in mind.
- Voltage - Input (Min): This must be equal to or lower than the voltage the solar panels produce, headroom recommended. Ideally this should be as low as possible, allowing the converter to work when the solar panels are not producing much voltage.
- Voltage - Input (Max): This must be equal to or higher than the maximum voltage the solar panel string can produce, headroom recommended.
- Voltage - Output (Min/Fixed): This must be equal to or lower than the minimum battery voltage, headroom recommended.
- Voltage - Output (Max): This must be equal to or higher than the maximum battery voltage, headroom recommended.
- Current – Output: This must be equal to or higher than the maximum current that can be produced by any complete solar panel (the entire PCB on one side of the satellite), headroom recommended. If each panel can produce 20 mA max and the maximum number of strings on any one panel is 2 then this value is 40 mA.
- Pay attention to the package design to make sure it can be soldered easy, SOT-23-5/6, 8-VSSop, and 8-SOIC or 8-SO are relatively easy to solder.
- Check the operating temperature to ensure it is within limits.

- C3 & C4: These are input and output filtering capacitors, respectively, whose value can be found in the application circuits of the datasheet of U3. Follow the guide for C1 & C2 to find this part and select the needed capacitance.
- Note: Adding more capacitors in parallel with C3 would not be a bad thing if there is room on the PCB, they will help stabilize the output from the solar panels to help the converter run more efficiently. 100 nF, 1, and 10 µF capacitors are always a good choice (100 nF is most important, then 1 µF, then 10 µF). You could add one of each or two of each room permitting.
- L1: This is the inductor that U3 uses to convert the input voltage to the output voltage. The value needed can be found in the application circuits of datasheet for U3. To find this part search Inductor on DigiKey and select Fixed Inductors. From there refine the search with the following filters:
- Packaging: Cut Tape (CT)
- Part Status: Active
- Inductance: Select the required inductance found in the datasheet of U3.
- Current Rating (Amps): This needs to be equal to or higher than the maximum output current of U3 (1 A for the example), headroom recommended. If U3 has a very high current rating, one that will never be achieved by the solar panels the maximum current that can be produced by any complete solar panel (the entire PCB on one side of the satellite) can be chosen.
- Current – Saturation: This needs to be equal to or higher than the maximum output current of U3 or any complete solar panel (1 A for the example), headroom recommended.
- Mounting Type: Surface Mount
- From here you can sort by price ascending and select a part, pay attention to the package size and ensure it is not too large.
- Attempt to find an inductor with the lowest resistance possible to maximize efficiency.
- Ensure the operating temperature is within limits.
- D7: This diode will typically have a recommended part within the datasheet which can be used, however, you may be able to find a low forward drop Schottky diode which will increase the efficiency of the converter. One of these should be used for D5/D6 which should be able to be reused so long as the max current of the diode is equal to or higher than the maximum current that can be produced by any complete solar panel with headroom (the entire PCB on one side of the satellite). If each panel can produce 20 mA max and the maximum number of strings on any one panel is 2 then this value is 40 mA. The reverse voltage standoff must also be equal to or higher than the maximum voltage of the batteries with headroom.

- R4 & R5: These resistors adjust the output voltage of the converter. R4 will typically be given in the datasheet of U3 as well as an equation to calculate the value of R5 for a desired output voltage. The higher these values are the more efficient the converter will be due to less current loss through the resistors, however U3 will typically have a max value for them due to noise and instability of the converter. For the example U3, R4 was given as 1 MΩ and the equation for Vout was given as Vout = 0.22 V ∗ (1 +

R4
R5

),

allowing you to calculate the needed value for R5. To find the needed resistors follow the same process as R1 and select the needed 1% resistance value. Table 3 gives the R5 values for different battery voltages for the example circuit. I would recommend buying a few resistor values around the theoretically needed value to tune the output voltage.

Table 3 – Resistance values for differing battery pack configurations for the example circuit.

Number of Cells | Resistance (kΩ)
1 Cell (4.2 V) | 54.9
2 Cells (8.4 V) | 26.7
3 Cells (12.6 V) | 16.9
4 Cells (16.8 V) | 11.8
- J4: This is an inhibit switch for the batteries, this will prevent them from accidental overcharge during storage which may lead to destruction of the cells, as well as ensure they do not activate until the inhibit is removed before launch. This should be a locking switch or jumper cable that is easily accessible on the outside of the payload.

This concludes the component breakdown for the DC/DC converter solar panel interface, if current from the solar panels stays within the limits of U3 all parts should be able to be recycled between payloads with different amounts of batteries in series by only changing R5, whose value for different batteries can be found in Table 3.

Linear Regulator: The next option for the interface between solar panels and energy storage is to use a linear regulator. This option is inefficient because a linear regulator wastes any voltage that is above its output voltage. However, it is simpler with fewer parts. To use this option the solar panels voltage must be higher than the battery voltage by typically at least 1.25 V, however the voltage should be higher, so the solar panels are still able to charge the batteries when they are not perpendicular to the light source which is when they produce their maximum voltage. Figure 13 shows the example circuit.

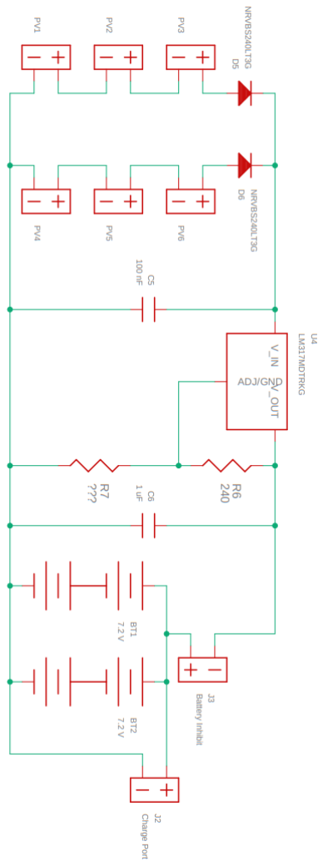
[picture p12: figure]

Figure 13 - Linear regulator interface between a solar input and energy storage

Component Breakdown: This circuit takes the voltage produced by the solar panels and outputs the maximum battery voltage to charge the batteries.

- U4: This part is the linear regulator which will produce the voltage needed to charge the battery. They have a dropout voltage (1.25 V in this example), which the input voltage needs to be higher than for it to produce the desired output voltage. To find these parts search Linear Regulator on DigiKey and select PMIC - Voltage Regulators – Linear, then use the following filters:
- Packaging: Bulk, Cut Tape (CT), and Tube
- Part Status: Active
- Output Configuration: Positive
- Output Type: Adjustable
- Number of Regulators: 1
- Mounting Type: Surface Mount
- Stock Status: In Stock
- Voltage – Input (Max): This value must be equal or higher than the maximum voltage of the solar panel string, headroom recommended.
- Voltage – Output (Max): This value must be equal or higher than the battery voltage you need to charge to, headroom recommended.
- Current – Output: This must be equal or higher than the maximum current that can be produced by any complete solar panel (the entire PCB on one side of the satellite), headroom recommended. If each panel can produce 20 mA max and the maximum number of strings on any one panel is 2 then this value is 40 mA.
- From here you can sort by price ascending and select a part with these considerations:
- The lower the dropout voltage, the more efficient the part will be
- These parts produce a lot of waste heat, so power must be taken into consideration. Within the datasheet of the part there should be a Maximum Output Current within the Electrical Characteristics table. It may have a few values at different input minus output values, and then a current will be given. You can calculate your input – output value by subtracting the output voltage of the linear regulator from the maximum string voltage form the solar panels. Using this you can see if the Maximum output current the part is able to supply around that voltage difference is higher than the maximum current that can be produced by any complete solar panel. Larger parts will provide larger maximum current values. DPAK and D²PAK are great packages for high power linear regulators.
- Ensure operating temperature is within limits.

- C5 & C6: These are input and output filtering capacitors, respectively, whose value can be found in the application circuits of the datasheet of U4. Follow the guide for C1 & C2 to find this part and select the needed capacitance.
- Note: Adding more capacitors in parallel with C5 would not be a bad thing if there is room on the PCB, they will help stabilize the output from the solar panels to help the converter run more efficiently. 100 nF, 1, and 10 µF capacitors are always a good choice (100 nF is most important, then 1 µF, then 10 µF). You could add one of each or two of each room permitting.
- R6 & R7: These resistors adjust the output voltage of the linear regulator. R6 will typically be given in the datasheet of U4 as well as an equation to calculate the R7 for a desired output voltage. The equation for U4 in the example is Vout = 1.25 V ∗ (1 +

R6
R7

),

allowing you to calculate R7 for a known output voltage, this is also the typical equation for 1.25 V dropout linear regulators. Table 4 gives the values for R7 for different battery voltages. You can use the guide for R1 to find the 1% resistor needed. I would
recommend buying a few resistor values around the theoretically needed value to tune the output voltage.

Table 4 - R7 values for different battery cell counts for the example circuit.

Number of Cells | R7 (Ω)
1 Cell (4.2 V) | 100
2 Cells (8.4 V) | 41.2
3 Cells (12.6 V) | 26.1
4 Cells (16.8 V) | 16.9

This concludes the component breakdown for the linear regulator interface between the solar panels and the energy storage. All parts should be able to be used for any payload, just ensure that the maximum current that is able to be supplied by any single side of the satellite in full sunlight is within the constraints of the linear regulator. To recap, for this to function the voltage the solar panels supply must be higher by at least 1.25 V then the output voltage which is the maximum battery voltage. However, the voltage should be higher than 1.25 V above the output to ensure the batteries will charge even when the solar panels are not perpendicular to the Sun.

Direct Linking: The last method for interface the solar panels with the batteries is by a direct linkage. This method may or may not be more efficient then a linear regulator, depending on some factors, but it is by far the simplest of the three. For this to work the open circuit voltage of a solar panel string must be the same or slightly higher than the battery voltage for the batteries to ever gain a full charge. This raises a safety issue, if the open circuit voltage is higher than the maximum battery voltage, the batteries run the risk of overcharging which will lead to a failure. To prevent this, the activation circuit, which will be outlined later, will passively activate to turn the payload on and drain the batteries. Figure 14 shows a direct linkage interface.

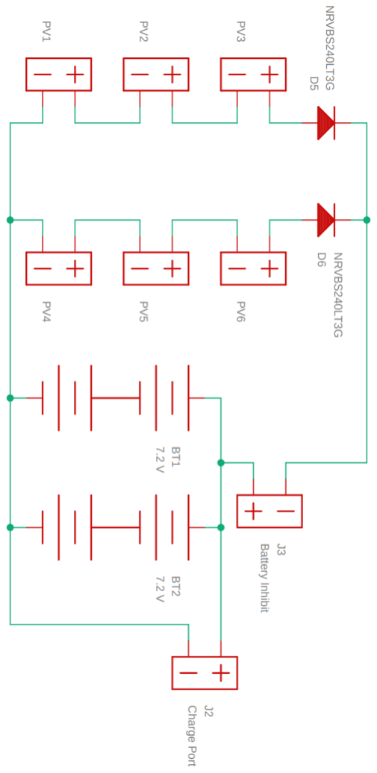
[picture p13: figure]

Figure 14 - Direct linkage interface between a solar input and energy storage

This interface can work because solar panels act like current sources. When the solar panel is illuminated the voltage of the panel string will increase until it is equal to the voltage of the batteries. Then it will begin behaving as a current source, sinking current into the batteries which charges them.

There are no needed components for this circuit, making it the cheapest as well. J3 prevents an overcharge case during storage, and after launch the activation of the payload will constantly drain the batteries, not allowing an overcharge failure. The solar panels must have an open circuit voltage equal to or slightly above the maximum battery voltage to allow the batteries to get close to a full charge before payload activation, allowing for a longer payload on time.

Payload activation

This circuit is meant to supply power once the batteries reach a certain state of charge, and then allow the current to continue to flow until the batteries have depleted to a certain, safe voltage, where the payload will then switch off to allow the batteries to recharge from the solar panels until their next activation. Figure 15 shows the activation circuit. The components will be discussed following the figure.

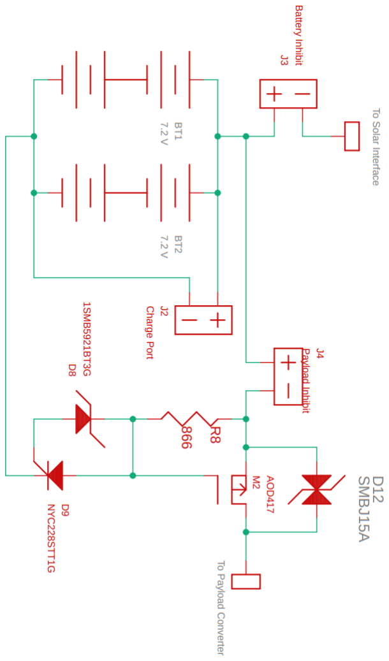
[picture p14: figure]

Figure 15 - Payload activation circuit

Component Breakdown: As an overview of the circuit, the MOSFET (M2) is normally off and will block current flow to the payload, keeping them off and allowing the batteries to charge from the solar panels. Once the batteries charge to a certain point, the Zener diode (D8) will break down and activate the SCR (D9). This will turn the MOSFET on and allow current flow to the payload, activating it. Resistor R8 establishes a holding current through D9, keeping it on until the batteries discharge to a certain point, where the holding current can no longer keep D9 on and D9 will close, closing the MOSFET.

- M2: This MOSFET must block the voltage of the fully charged battery voltage, as well as be in the on state with a logic level at its gate. This is the same part that is used for M1 in the RockSat section and is interchangeable between the two payload types. The guide for selecting a different MOSFET can be followed in the guide for M1.
- D12: This is a protection diode for the MOSFET, the same as D4 on the RockSat example circuit.
- D9: This is the SCR that will turn the MOSFET on and off. This is the same part as D3 in the RockSat section and is interchangeable between the two payload types. As a reminder, this SCR must block the voltage of the fully charged batteries in its off state. This part should have the lowest holding current possible to minimize energy losses in the payload. The guide for selecting a different SCR can be followed in the guide for D3.

- D8: This is the Zener diode that will activate the SCR. Zener diode will reverse conduct once a certain voltage threshold is reached, much like the TVS diode. To find the needed breakdown voltage value for this you need to select the voltage you wish to activate the payload at. This should be higher than the nominal voltage of the batteries (3.7 for each cell in series) but lower than the maximum charge voltage of the batteries (4.2 V for each cell in series). This is because over multiple cycles the batteries will not be able to charge to their maximum voltage as they slowly degrade, and if the Zener diode breaks down at that voltage it will never be able to reach its breakdown threshold. To find a Zener diode search Zener of DigiKey and select Diodes - Zener – Single then select the following filters:
- Packaging: Cut Tape (CT)
- Part Status: Active
- Mounting Type: Surface Mount
- Stock Status: In Stock
- Supplier Device Package: I would recommend selecting SMB and SMC for solderability, however this may limit the breakdown voltages available to you, so if you do not find a voltage usable by you after you select this filter you could undo it and go with another package.
- Voltage - Zener (Nom) (Vz): This is the voltage the Zener diode will break down at. You want this number plus the Voltage - Gate Trigger (Vgt) (Max) of the SCR you selected to be in between the nominal and maximum battery voltage. The SCR gate trigger voltage for the example is 0.8 V, and with a 6.8 V breakdown Zener this will give an activation voltage of 7.6 V, above the 7.2 V nominal voltage but below the 8.2 V maximum voltage.
- Ensure the operating temperature is within limits.
- R8: This resistor establishes the holding current for the SCR and determines at what state of charge the SCR will turn off. The guide for R1 can be followed to select this 1% resistor. To determine the resistance value, you need to know the Voltage - On State (Vtm) (Max) and Current - Hold (Ih) (Max) of the SCR. The batteries should be turned off at or above 3 V for each cell to keep the batteries healthy, 3 V per cell was selected for the example. This gives a total voltage at turn off of 6 V. From the 6 V subtract the Voltage - On State (Vtm) (Max) which was 1.7 V, giving 4.3 V. At 4.3 V the current must be equal to the Current - Hold (Ih) (Max) to turn the SCR off, so R =

V
I

=

4.3 V
5 mA

=

860 Ω (866 Ω was chosen as a standard 1% value which will turn the payload off just before 3 V which is preferred over slightly lower than 3 V). This needs to be prototyped and tested, I would highly recommend buying a few resistor values around this theoretical resistance (both higher and lower) in case of variances between the SCRs.

This concludes the component breakdown for the passive payload activation which will activate at a certain battery voltage threshold and then turn off before the state of charge of the batteries goes too low. Prototyping is important with this circuit as it may take a few resistor values to tune the turn off voltage of the batteries.

Payload Converter

The next section is the converter for the different payloads and subsystems on board the satellite. There are two ways to accomplish this. Multiple converters may be needed as different payloads may require different voltages. If two subsystems require the same voltage, they may be put onto the same converter rail to save PCB space if the converter is able to supply the current. If the payload can support a wide input range that is inclusive of the minimum and maximum voltages of the battery pack, such as the amplifiers and VIPE transformer on the Aether payload, then they may be directly connected to the payload activation circuit. If the payload has a range of accepted voltages but conversion is still needed, the center value is a good target to aim for.

DC/DC Converter

The most efficient method to the this is to use a DC/DC converter to convert the changing battery voltage into a constant output voltage that is usable by the subsystem. This is the same concept as the DC/DC converter interface between the solar panels and the batteries. Figure 16 shows an example circuit with recommended parts to build this DC/DC converter.

Figure 16 - DC/DC converter for battery voltage to stable payload voltage conversion

Component Breakdown: This circuit accepts the full voltage range of the batteries as shown in Table 5 (using 3 V as the minimum for each cell) and convert that changing voltage with battery state of charge into a stable output voltage that is usable by a payload or payloads. The selected part is a Step-Up/Step-Down converter with a wide input and output. It can accept 3 to 25 V input, greater than the entire range of all Minimum and Maximum Voltages for each battery pack. It can output 1.2 to 35 V at 1.5 A. This converter should be able to handle most applications needed by small satellites.

Table 5 - Minimum and maximum voltage for each battery cell count

Number of Cells | Minimum Voltage (V) | Maximum Voltage (V)
1 Cell | 3 | 4.2
2 Cells | 6 | 8.4
3 Cells | 9 | 12.6
4 Cells | 12 | 16.8

- U5: This is a step-up/step-down converter, meaning that it can accept a lower, higher, or equal input voltage then its set output voltage. This was chosen in case the voltage range of the battery cells started higher than the needed voltage then drops lower than the needed voltage as the battery discharges. This may be the case if 3.3 V (common for logic devices) is needed and one cell is being used, the voltage starts higher at 4.2 V but as the battery discharges it will eventually drop lower than the output. The SHDN ̅̅̅̅̅̅̅̅ is

intentionally left disconnected as the datasheet says to leave the pin floating to turn the converter on. To find these parts search Converter on DigiKey and select PMIC - Voltage Regulators - DC DC Switching Regulators, then select the following filters:
- Packaging: Bulk, Cut Tape (CT), and Tube
- Part Status: Active
- Function: Note, choose all the selections with Step-Up, Step-Down, or Step-Up/Step-Down if separated by a comma, there may be multiple (e.g. select Radiometric, Step-Up if Step-Up is needed).
- If the Maximum Voltage of your chosen pack is below your needed output voltage: Step-Up
- If the Minimum Voltage of your chosen pack is above your needed output voltage: Step-Down
- If the voltage requirement is between the Minimum and Maximum Voltages of the chosen pack: Step-Up/Step-Down
- Output Configuration: Positive
- Output Type: Adjustable
- Number of Outputs: 1
- Voltage – Input (Min): Everything equal or lower than the Minimum Voltage of your chosen cell.
- Voltage – Input (Max): Everything equal or higher than the Maximum Voltage of your chosen cell.
- Voltage - Output (Min/Fixed): Everything equal or lower than the required output voltage.
- Voltage – Output (Max): Everything equal or higher than the required output voltage.
- Current – Output (Max): Everything equal or higher than the current requirement of the payload or payloads.
- Mounting Type: Surface Mount
- You can now sort by price ascending and select a part, pay attention to the package to ensure if can be soldered easily (such as 8-SO). The additional components needed will be in the typical application section along with formulas to calculate certain values. The circuit will most likely not look like the example if a new IC is chosen.

- C7 & C10: These are the input and output filtering capacitors for the converter. Follow the guide for C1 & C2 and select the capacitance value listed in the typical application section of U5.
- Note: Adding more capacitors in parallel with C7 would not be a bad thing if there is room on the PCB, they will help stabilize the input to the converter to help the converter run more efficiently. 100 nF, 1, and 10 µF capacitors are always a good choice (100 nF is most important, then 1 µF, then 10 µF). You could add one of each or two of each room permitting.
- R8, C8, & C9: These are passive components needed by U5 that were listed in the typical supplications section. Use the guide for R1 and C1 & C2 to select them and select the required capacitance. If a different U5 chip is chosen these may or may not be required, check the typical applications section.
- L2: This inductor is required by U5 to convert the voltage. Follow the guide for L1 to select this, ensure the maximum current and saturation current are higher than the Current – Output (Max) of U5 or the required current by the payload or payloads.
- D10: This diode is needed by U5 for operation. Follow the guide for D5 & D6 to select this diode, it should be a low drop Schottky to keep the efficiency of the converter as high as possible.
- R9 & R10: These are the feedback resistors needed by U5 to sense and adjust the output voltage as necessary. For the example part R10 was given. The needed output voltage is known from the part requirement so the formula for R9 is given as R9 =

R10(Vout−1.2)
1.2−R10(0.2 µA)

Values of R9 for common voltage are listed in Table 6. Use the process to select R1 to select these resistors. I would recommend buying several parts around the theoretical R9 to tune the output voltage for the specific U5 chip (requires testing).

Table 6 - R9 values for common voltages for the U5 part of LT1961EMS8E#PBF

Output Voltage (V) | R9 (kΩ)
3.3 | 17.4
5 | 31.6
9 | 64.9
12 | 90.9
15 | 115
20 | 158
25 | 200
30 | 243
35 | 280

This concludes the component breakdown for a DC/DC Converter for a payload or payloads. The selected component for U5 is a wide input and wide output device which should be able to handle most needs in small satellites. Multiple converters may be required for multiple payloads with different voltage needs. If two payloads have the same voltage requirements it will save space and design work to have both payloads using one converter if the currents are within the limits of the converter.

If additional current is needed by the payload and another IC for U5 cannot be found with current capabilities high enough it is possible to place multiple converters in parallel. The issue with doing this is the converters will not all supply the exact same voltage, leading one converter to ‘feed’ current into the other converter or converters. To prevent this a protection diode should be placed after the output filtering capacitor (C10) which could be the same diode as D10 (it does not replace D10, two diodes are now needed). This will mean that the output voltage will need to be the required voltage plus the forward drop of the additional diode.

The other option to supply higher current or simplify the circuit is to find a prebuilt DC/DC converter. These will be more expensive than building a circuit such as Figure 16. To do this search DCDC on DigiKey and select DC DC Converter (there may be 2 options, select the one with a higher number of items), then select the following filters:

- Packaging: Box, Cut Tape (CT), & Tube
- Part Status: Active
- Number of Outputs: 1
- If multiple voltages are needed you may be able to find a multioutput converter that meets your requirements, if so select more outputs to search
- Voltage – Input (Min): Everything equal or lower than the Minimum Voltage of your chosen cell.
- Voltage – Input (Max): Everything equal or higher than the Maximum Voltage of your chosen cell.
- Voltage – Output 1: Select the required output voltage for the payload.
- Current – Output (Max): Everything equal or higher than the current required by the payload or payloads.
- Mounting Type: Surface Mount & Through Hole
- Part Status: In Stock
- Sort by price ascending and find a part which will work for your payload, be mindful of the package design as some can be very difficult to solder.
- Ensure the operating temperature is within limits.

Linear Regulator

Like the linear regulator linkage between the solar panels and batteries, a linear regulator can be used to regulate the battery voltage to a constant output voltage for a payload. This will be less efficient versus using a DC/DC converter, however the advantages of using this are more prevalent for payloads. DC/DC regulators can produce some noise in their output voltages since they are switching regulators. To dampen this noise filters can be added to the output in addition to the output capacitor, however often there is still some noticeable noise. For noise sensitive payloads, such as a communications circuit, the noise may be too high for optimal operation. Because of how they operate, linear regulators provide a smooth voltage rail which is typically very low noise. This can be very useful for noise sensitive payloads.

To use a linear regulator the minimum voltage of the chosen battery pack (given in Table 5) must be 1.25 V higher than the needed output voltage. Values lower than 1.25 V exist but will not be examined in the example circuit. A note will be made of how to search for low-drop linear regulators. If the battery voltage drops too low over the battery discharge cycle and a linear regulator is necessary a step-up converter will need to convert the battery voltage at least 1.25 V higher than the needed output voltage, then a linear regulator can regulate the output from the DC/DC converter to the voltage needed by the payload. Figure 17 shows an example payload converter using a linear regulator.

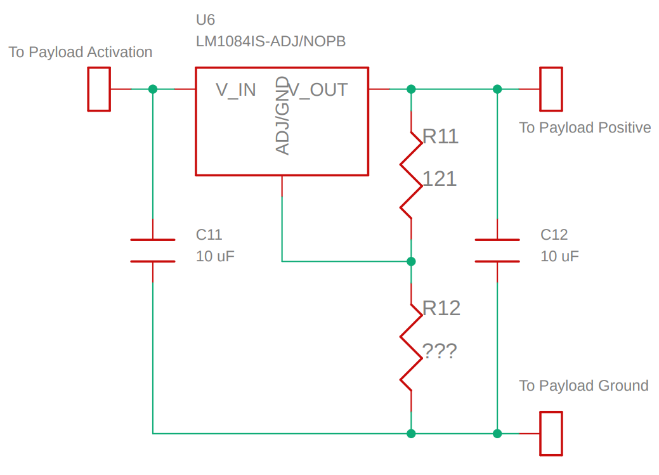
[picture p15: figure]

Figure 17 – Linear regulator for battery voltage to stable payload voltage conversion

Component Breakdown: The linear regulator (U6) selected is a very large package with a lot of power dissipation, meaning it can supply a lot of output current. This large of a package may not be needed if the payload does not require much power, in which case I would recommend selecting a lower power linear regulator since this is quite large and expensive. It can accept up to 29 V which is greater than the battery voltage maximum range and can output 1.25 – 27.5 V at 5 A (Note, this is if the difference between input and output voltage is only 1.25 V, the minimum difference possible). This will produce a clean, low noise output voltage.

- U6: This is the linear regulator which will convert the input voltage to the needed output voltage by turning the excess voltage into waste heat. This part may get warm or even hot during normal operation. Excessive waste power may overheat and possibly fail the device. The same process to select U4 may be taken to find these parts with the following amendments:
- Voltage – Input (Max): This value must be equal or higher than the maximum voltage of the batteries (Table 4).
- Voltage – Output (Max): This value must be equal or higher than the needed voltage for the payload.
- Current – Output must be equal to or higher than the needed voltage by the payload, however, pay attention to the Maximum Output Current within the Electrical Characteristics table which shows different output voltages with different differences between input and output voltages, as noted in U4. Use the maximum battery voltage to find the maximum difference between the input and output voltages of the linear regulator.
- C11 & C12: These are the input and output capacitors to filter and stabilize the input and output of the linear regulator. These values may be different if a different U6 component is selected. The suggested values will be listed in the typical application section of the datasheet for U6. The process to select C1 & C2 can be followed to select these.
- Note: Adding more capacitors in parallel with C11 would not be a bad thing if there is room on the PCB, they will help stabilize the input to the converter to help the converter run more efficiently. 100 nF, 1, and 10 µF capacitors are always a good choice (100 nF is most important, then 1 µF, then 10 µF). You could add one of each or two of each room permitting

- R11 & R12: These resistors set the output voltage of the linear regulator. The recommended value for one of these resistors will be given in the typical applications section of U6, as well as a formula to calculate the other resistor. R11 was given as 121 Ω. Typically for 1.25 V drop linear regulators (the example U6 included) the formula is Vout = (1.25 V) ∗ (1 +

R12
R11

). The process to choose these resistors can be followed from

R1. Common values that may be needed for R11 are listed in Table 7. I would recommend buying several parts around the theoretical R11 to tune the output voltage for the specific U6 chip (requires testing).

Table 7 - R12 values for common voltages for the U6 part of LM1084IS-ADJ/NOPB (and typical 1.25 V dropout linear regulators)

Output Voltage (V) | R12
3.3 | 200 Ω
5 | 365 Ω
9 | 750 Ω
12 | 1.05 kΩ
15 | 1.33 kΩ
20 | 1.82 kΩ
25 | 2.32 kΩ
27.5 | 2.55 kΩ

This concludes the component breakdown for the linear regulator payload voltage converter. The selected linear regulator in the example should have enough power dissipation and voltage possibilities to meet the requirements of most payloads. If space is limited or not that much current is required I would recommend finding another part for this linear regulator, otherwise it is by far over-engineered.

The following 4 figures show complete configurations that are possible using this guide, all using 2 cells in series (1 – 4 is usable with all designs and components with some resistor values needing adjustments). Note the addition of J4 in the small satellite examples, this is another inhibit to add to the payload to ensure the payload or payloads are not activated by the solar panels before launch. All the boxed components are the only components that need to be changed depending on the battery pack voltage if all the other components are left the same and they also are within the current limits of the payload or payloads.

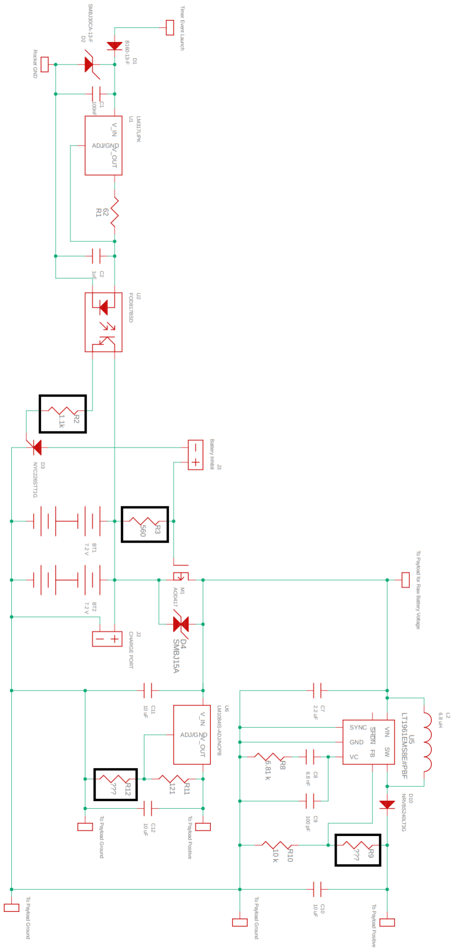
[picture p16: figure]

Figure 18 – Example RockSat or like-flight circuit designed from the information contained in this guide.

Figure 19 - Small satellite example circuit designed from this guide using a DC/DC converter interface between the solar panels and batteries.

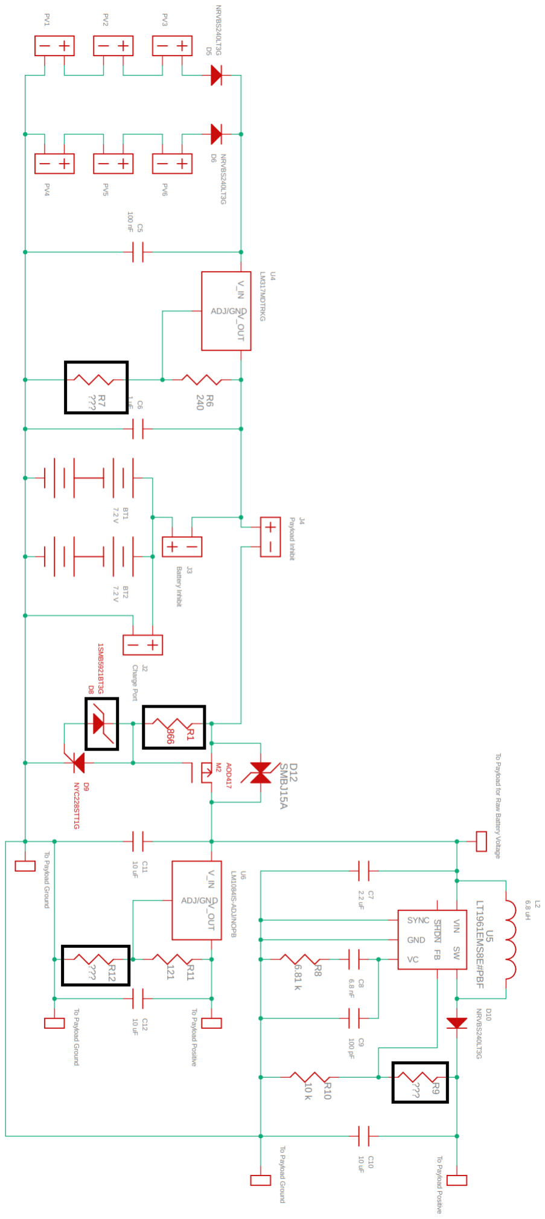
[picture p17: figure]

Figure 20 - Small satellite example circuit designed from this guide using a linear regulator interface between the solar panels and batteries.

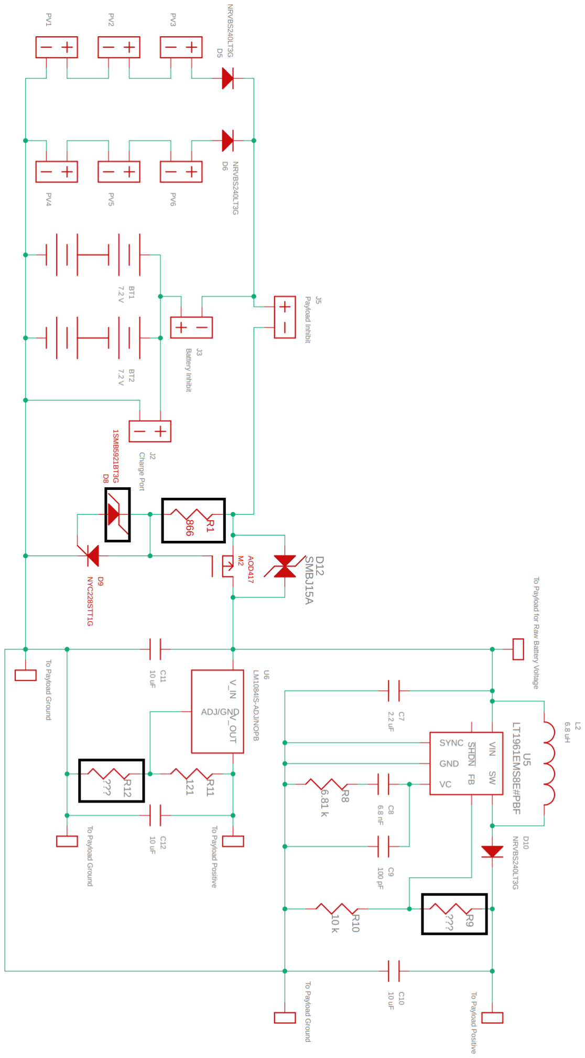
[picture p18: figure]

Figure 21 - Small satellite example circuit designed from this guide using a direct interface between the solar panels and batteries.

PCB and Other Considerations

This is a brief section about designing a PCB where I will highlight a few points. I would recommend using Advanced Circuits (www.4pcb.com) for ordering PCB, you can easily export Autodesk Eagle (which I would also recommend using to design the circuit and PCB, free from Autodesk with a student license) designs by going to File > Generate CAM Data. These files can then simply be zipped together and given to Advanced Circuits to run their Free DFM checker to ensure there are no electrical or manufacturing issues with the board. After the results are received from that, if nothing needs to be changed, you can give them the board number and they will manufacture the board.

- Before designing the PCB and especially before ordering it I would highly recommend ordering all the parts required to make the board and prototype and test the design on vector board. This is to ensure any issues are worked out before ordering the board which could prove costly if a revision is needed.
- For the RockSat example, all the inhibits should be locking switches or add-before-flight jumpers. For the small satellite examples all the inhibits should be locking switches or add-before-flight jumpers in series with the contact switches that close when the payload is deployed.
- These PCB should be designed as 2 layers, the traces are not too complicated as there is not too much logic needed, this will also reduce the price of manufacturing the PCB by a considerable amount.
- Keep solderability in mind, space the parts out enough to where you will easily be able to maneuver a soldering iron and achieve a good solder joint.
- Think about other parts around as well, you may be able to easily solder in a resistor if you do it before you solder an IC, but if you need to change the resistor after testing it may be difficult.
- For best operation filtering capacitors should be located as close as possible to the IC that requires them.
- For rails (nets in the schematic that have a lot of connections, such as raw battery voltage and ground) make a plane on the top and bottom of the board for better performance.
- Ensure there are no floating islands in the plane and the isolation for the planes are large enough (~20 mils).
- Traces should not be larger than the smallest solder pad on either end of the connection. ~20 mils is a good starting point for trace width.
- Excessively large traces can cause troubles when soldering, but they need to be large enough to able to handle the current that will flow through them.
- Datasheets should contain recommended soldering pad layouts (if not you can find another part with the same package from a different manufacturing which may contain the recommended layout).

- Often there are multiple layouts for different soldering methods (reflow, wave, etc.) if there is no specific hand soldering layout choose the layout with the largest pads or oversize the pads if you believe they are still too small to hand solder.
- Silkscreen is free, make sure it is large enough to read and label everything on the board that you think you will need, add test points if you think you may need to test certain areas or function of the board.
- Test points can just be single pads which a lead can be soldered onto or probed by a multimeter.
- Use lead solder, lead free solder can whisker and cause short circuits in space applications.
- Use plenty of flux when soldering, just ensure you give the board a thorough cleaning with isopropyl alcohol afterwards, there should be no flux residue (orange color) left. Use an acid brush to wipe the alcohol on the board, paying special attention to solder joints and underneath ICs.
- A good solder joint resembles a smooth filet of solder from the top of the component to the far side of the solder pad, as shown in Figure 32. There is too much solder if the joint starts looking spherical, use a solder wick to remove the solder and resolder the joint.

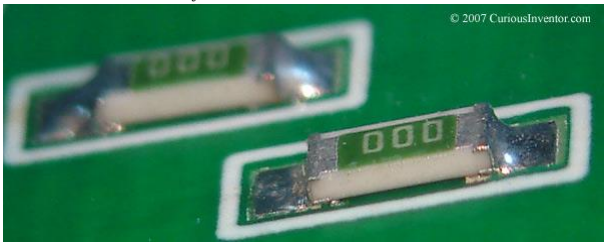
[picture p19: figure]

Figure 22 - Example of a good solder joint for an 0805 resistor – Curious Inventor

- Do not use electrolytic capacitors for space application. Look like a can, in Figure 33

Figure 23 - Electrolytic capacitor – DigiKey

- For electronic components DigiKey and Mouser are the two big companies, you can compare parts and prices from both if you desire.
- For electronic parts a commonly use parts from:
- Analog Devices
- AVX Corporation
- Bourns Inc.
- CUI Inc.
- Diodes Incorporated
- Infineon Technologies
- KEMET
- Keystone Electronics
- Linear Technology
- Littlefuse Inc.
- Maxim Integrated
- Microchip Technology
- Monolithic Power Systems Inc.
- Murata
- Nexperia
- Ohmite
- ON Semiconductor
- Panasonic
- Recom Power
- Rohm Semiconductor
- Samsung
- Stackpole Electronics Inc
- Taiyo Yuden
- TDK Corporation
- TE Connectivity
- Texas Instruments
- Toshiba
- United Chemi-Con
- Vishay
- XP Power
- Yageo

- When ordering parts always order more then you need for the circuit.
- For small passive components (resistor, capacitor, and inductor) I will typically order at the next price break, usually at 10 components, though if the part is very cheap I often order 100 components as well.
- For larger and more expensive ICs I typically buy 1-3 extra depending on the price.
- Use Silicone RTV to strain relief the connection between wires and the board after final integration. This will help absorb vibrations during launch.

The following figures are the electrical designs from the Aether and CACTUS – Hermes 3.0 missions to use as examples:

Figure 24 - Aether power board schematic. Only linear regulators and raw battery voltage were used for the payloads. Note D6 and D7 are status LEDs to give us a visual indication that power is flowing through the system and the high voltage inhibit is take out, respectively. Note, the U10 system allows the Pi to enable the high voltage payload (Appendix).

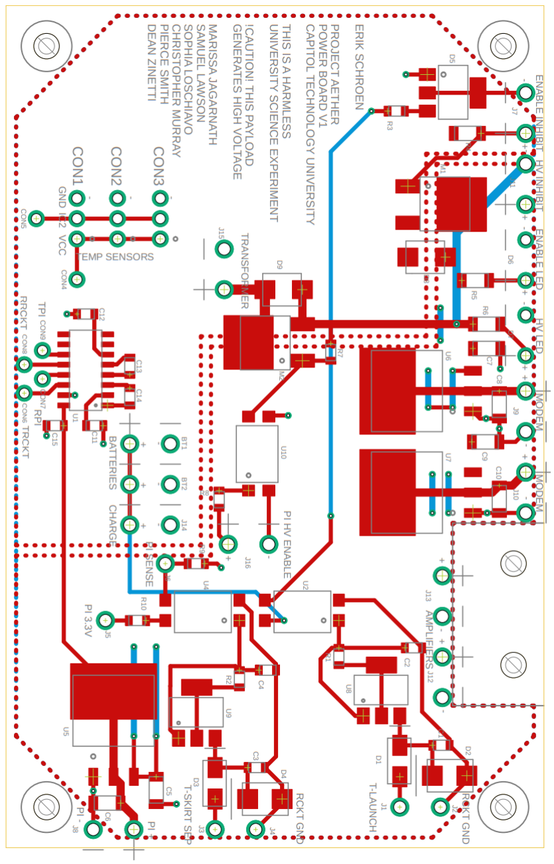
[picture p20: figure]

Figure 25 - Aether power board PCB design, the red and blue dotted line are the boundary of the battery voltage/5V rail and ground plane respectively.

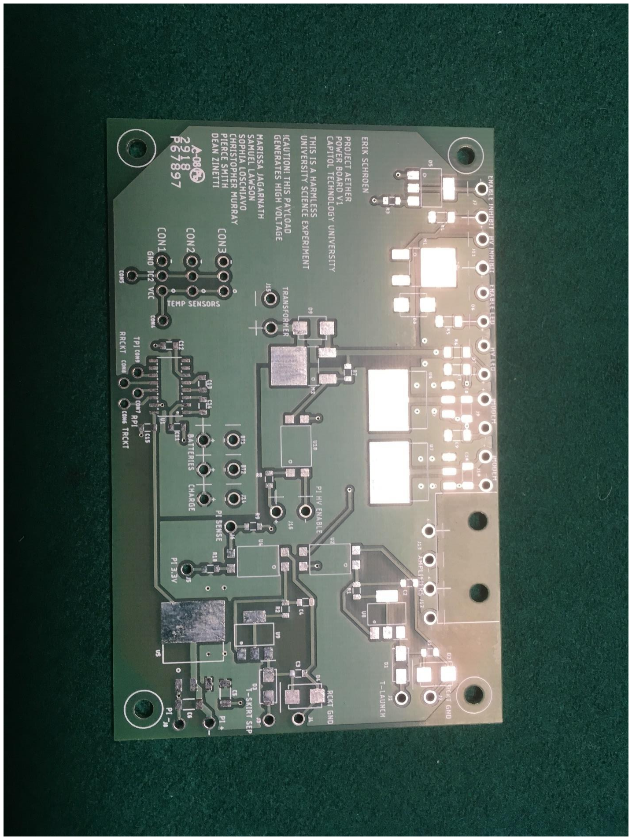
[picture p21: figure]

Figure 26 - Aether power board unpopulated PCB

Figure 27 - Aether power board populated

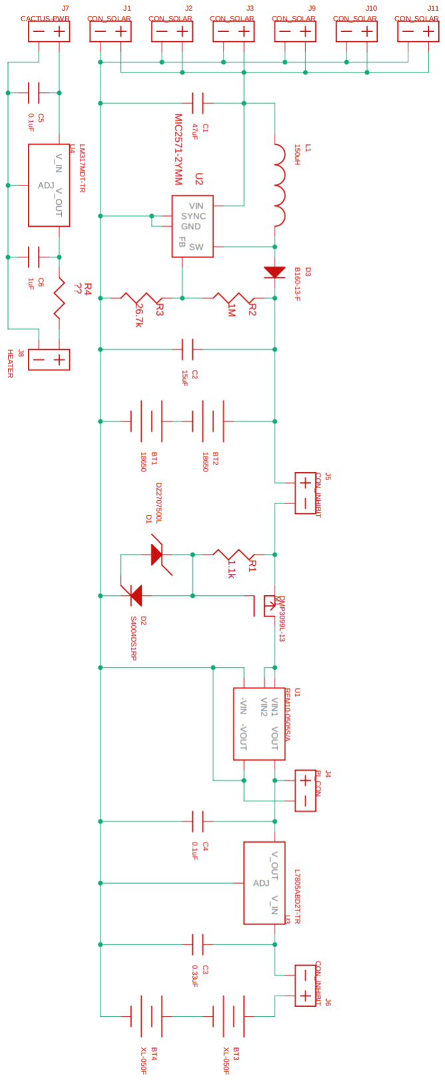
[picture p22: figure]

Figure 28 - CACTUS - Hermes 3.0 power board schematic. Only linear regulators and raw battery voltage were used for the payloads. A custom and prebuild DC/DC converter as well as a 5 V linear regulator were all used.

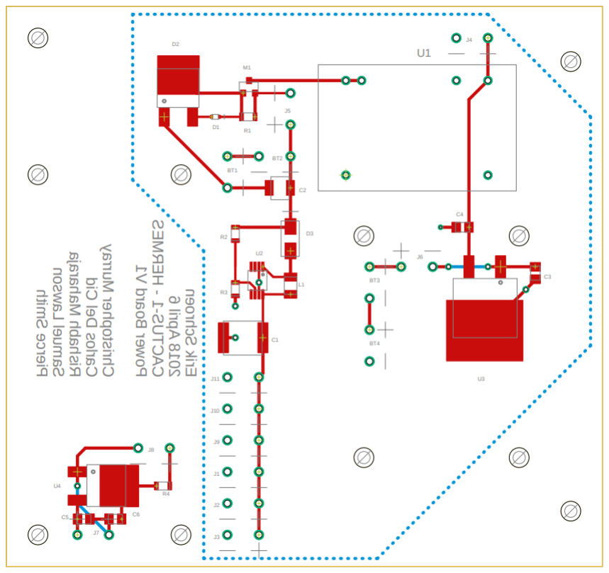
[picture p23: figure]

Figure 29 – CACTUS – Hermes 3.0 power board PCB design, the blue dotted line is the ground plane. This design used PC 104 standard.

Figure 30 – CACTUS – Hermes 3.0 power board unpopulated PCB

References/Additional Reading

Bouwmeester, J. Gill, E. Langer, M. (2016). Survey on the Implementation and Reliability of CubeSat Electrical Bus Interfaces. Springer.

Burt. R. (2011). Distributed Electrical Power System in CubeSat Applications. Utah State University.

Clark, C. (n.d.). Huge Power Demand…Itsy-Bitsy Satellite: Solving the CubeSat Power Paradox. 24th Annual AIAA/USU Conference on Small Satellites.

Doering, T. J. (2009). Development of a Reusable CubeSat Satellite Bus Architecture for the Kysat-1 Spacecraft. University of Kentucky.

Erb, D. M. (2011). Evaluating the Effectiveness of Peak Power Tracking Technologies for Solar Arrays on Small Spacecraft. University of Kentucky.

Lim, T. M. (2016). A Modular Electrical Power System Architecture for Small Spacecraft. University of Kentucky.

Notani, S. A. (2011). Development of Distributed, Scalable and a Flexible Electrical Power System Module for CubeSat and Small Satellites. North Carolina State University.

Smith, R. P. (2018). CACTUS-I Design Documentation and Future Guidance. Capitol Technology University.

Appendix

Custom Battery Charger

If you are going to use this charging circuit, the battery should constantly be monitored and disconnected immediately upon reaching the maximum voltage for the pack and current approaches zero. These are all through hole components, so this can be built on vector board for ease of population. Note the part number is given for R1, this is because this needs to be a high-power resistor. This charger will charge the batteries at 500 mA, R1 can be adjusted for a slower charging rate and may allow a standard through hole resistor to be used, I would not recommend going any higher (I =

1.25 V
R1

, ensure you calculate the power and check the resistor used is rated

at a high enough power). The values for R3 for the different battery packs is given in Table 8 (V = 1.25 V ∗ (1 +

R3
R2

)). A potentiometer could also be used in place of R3 to allow any output

voltage to be set, with no battery attached to the output use a voltmeter to read the output voltage and adjust the potentiometer until the desired voltage is reached (5 kΩ pot is a common value and will allow you to charge at greater voltages than 4 cells, the higher the turn count the greater the accuracy, I would use something like PV36W502C01B00). Ensure that during charging the potentiometer is not changed. Before connecting the charger to the battery pack always connect the power supply and ensure the output voltage is close to the maximum voltage of the battery pack (slightly lower is better than higher). Take caution when using this circuitry. Ensure at the end of the charge the current into the battery begins to drop off as the voltage approaches the setpoint value.

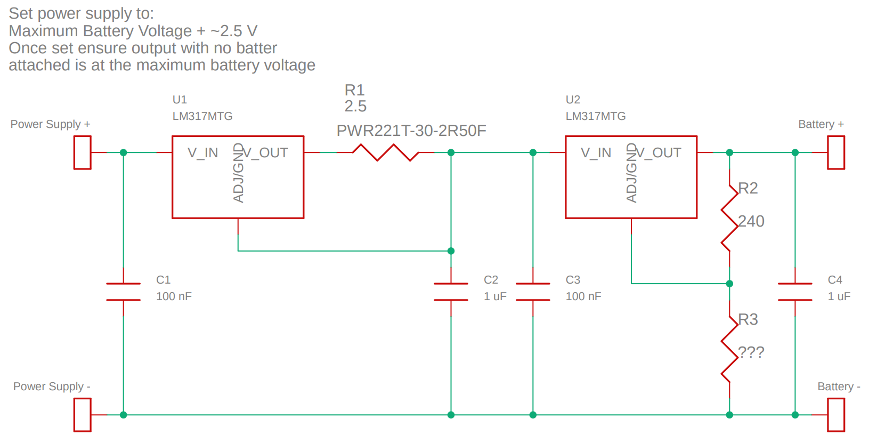
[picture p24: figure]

Figure 31 - Custom battery charger using 2 linear regulators, one in constant voltage and the other in constant current configurations.

Table 8 - R2 values for differing 18650 series cell counts.

Cells in Pack | Power Supply Voltage Minimum (V) | R2
1 Cell (4.2 V) | 6.7 | 562 Ω
2 Cells (8.4 V) | 10.9 | 1.37 kΩ
3 Cells (12.6 V) | 15.1 | 2.15 kΩ
4 Cells (16.8 V) | 19.3 | 2.98 kΩ

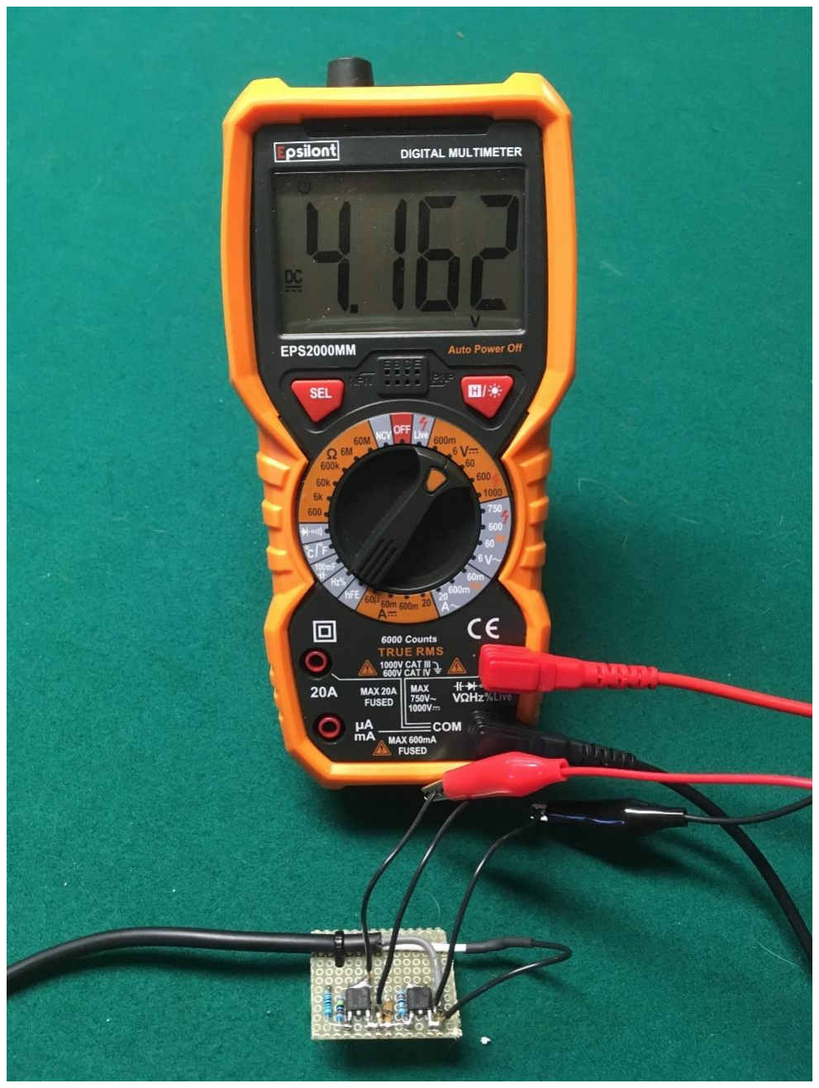
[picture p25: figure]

Figure 32 - Prototype board (not using listed part numbers but same functional parts) set up in a 1 cell configuration showing output voltage. A 19.5 V DC wall outlet converter is wired in from the left to provide power, allowing the board to be reconfigured to up to 4 cell charging (possible due to power because current was lowered to 100 mA). Total build time was around 1 hour.


Figure 33 - Closeup of prototype board.

Payload Activation from Pi

Figure 34 - Method for activating a payload from the control of a Pi (or Arduino etc.)

The circuit shown in Figure 34 will allow a processor to control when power flows to a payload. The circuit functions in the same way the as the power activation circuit for small satellites as previously described, but instead of being triggered by voltage it is turned on by a logic input from a processor. For this example, the Pi input was 3.3 V, so R14 was chosen as 133 to limit the input current to the forward current into the optocoupler to ~20 mA (To find this take the input voltage and subtract the forward LED drop found in the optocoupler datasheet then divide by the desired current to find the resistors, for a 5 V logic input a 191 Ω resistor should be used). R13 should limit the current through the BJT of the optocoupler to safe currents. D11 is a protection diode like D4.

Payload Converter Filters

If the output of the payload converters is too noisy for the system and using a converter to boost the voltage higher, then using a linear regulator to reach the desired output voltage, as discussed previously, is undesirable, then filters will need to be used. Capacitors are the most basic filters, sometimes adding capacitance to the output of the converter can greatly help with noise. If a 1 µF capacitor is used on the output I would recommend adding a 10 µF in parallel for example and observing the noise or doubling up on 1 µF capacitors in parallel. The most common filter for power supply noise reduction is the Pi Filter. To test the effectiveness of this filter, observe the voltage before filtering on an oscilloscope, then add the filter and re-observe. If the noise is still too high it is possible to cascade Pi filters, however their effectiveness will begin to decrease. Figure 35 shows a Pi Filter. Determining the values to this filter can be tricky but 10 -100 µH and 1 – 10 µF is a good starting point (order a couple values to test).


Figure 35 - Pi Filter

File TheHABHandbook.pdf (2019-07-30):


The High Altitude Handbook is a product by Ian Hastings.

@ 2018 Ian Hastings, all rights reserved


Acknowledgements: HAB payload development was supported by grants from the Maryland Space Grant Consortium (MDSGC).

uploaded July 2019

# The HAB Handbook

# By Ian Hastings

Contents

Introduction
What is Systems Engineering?
To talk about systems engineering, we must first define what a system is. A system is defined as anything that is composed of other components. For example, a car is a system. It’s made up of a chassis, an engine, suspension, etc. Breaking down systems into their components is the heart of systems engineering.

Systems Engineering is a robust method of designing, creating, and operating a system. The method relies on identifying and quantifying the requirements and goals, creating various designs and selecting the best design, and in the end, verifying that the design meets all goals and requirements and goals.

Why use Systems Engineering?
Without the use of systems engineering, large projects suffer where several independent groups made the components had issues integrating with each other and often the system created from the components did not fulfil the initial function and were often unusable. On top of that, missions that don’t utilize robust systems engineering principles tend to spend more money, go past their deadlines and don’t perform as well.

Example:
For example, if we were building a car, we cannot design and create each component one after the other, we must design two parts at the same time, like the chassis and the engine. If the group who was working on the chassis, changed the dimensions of the chassis for some reason, it may impact how the engine fits into the car. Without systems engineering overhead, this issue might go unseen until final integration where the engine would not fit. This mistake would cause one or both groups to have to go back and redesign and remake their components to make them fit, causing a massive loss of time and money for the project.

However, this situation is easily avoidable, with a systems engineering architecture in place, a systems engineer can monitor the entire process and make sure that each component is meeting its requirements and making sure that each component and interface with other. In this example, a systems engineer would see the change in size of the chassis, and either make the chassis team keep the original design or go to the engine team and give them new interface requirements before the system is complete.

What is HAB?
High Altitude Balloons, frequently abbreviated as HAB, are simply very large latex balloons that are filled with Helium in order to carry a payload to a high altitude. HAB are frequently used by institutions like NOAA and NASA for weather and climate measurements, as the most accurate method of gauging temperature, moisture and pressure of the local atmosphere is to release high altitude balloons to physically measure the data. HAB can easily fly into what is known as “Near Space” Which is a level in the atmosphere where the pressure is so low that humans cannot survive, and the environment is highly similar to being in space. These balloons can fly up to 120,000 feet into the air and frequently reach 100,000 feet. Upon reaching these altitudes, the low pressure causes the balloon to expand so much that it bursts, causing the payload to freefall and parachute safely down to the ground for recovery.

These HAB launches are also used as a low-cost method of getting to near space for science missions. Because it doesn’t cost much, these missions can be launched frequently and with higher risk payloads without fear. These payloads are frequently in the 1-2-pound range and are very small form factor, much like a CubeSat and are controlled by consumer grade microprocessors and sensors, like Raspberry Pi or Arduino. Most launches fly many different payloads at the same time in order to maximize the benefit of 1 launch and each payload is tied to the balloon through the main payload string.

Example:

For example, Cloud360 was a HAB payload designed to take PH measurements of nearby atmospheric moisture as well as take continual 360-degree video in order to corollate the PH to a specific cloud or cloud type. The mission was designed, built, and tested in one month by a group of visiting Brazilian students. The mission flew a total of 4-5 times in total and was fully successful in all but 1 launch. The payload was tied into the main payload string before launch and flew to 100,000 to 120,000 feet above sea level, constantly taking in 360-degree video and using a spinning spool of PH paper to measure the PH of clouds that the payload flew through. In total, the mission cost around 300 dollars to create, and the major cost factor was the $220 360-degree camera that was used. The mission highlights just how easy it is to get good useful science data from a HAB launch for a very low cost.


System Design Process
What is System Level Design?


System Level design is the process of breaking down a systems into subsystems. It is extremely useful for complex projects because it allows the project to be separated into subsystems that can be designed and built in parallel to each other, rather than working on a system as a whole. Each subsystem has its own requirements and interfaces that are dictated by the system’s requirements and goals.

Example
For example, a car isn’t designed and built as a whole system. It’s much more efficient for them to split up the car into subsystems. You can break the car down into a chassis, an engine, a crew cabin and drive system. Each subsystem will have requirements, like the chassis might have to be a certain size to fulfil the mission requirements. Furthermore, there are interface requirements for subsystems that meet, like the chassis might have to have mounting brackets for the engine to sit in.

System Modeling
Modeling a system is done in two different ways. The first method is the hierarchical diagram of the system from the top down. This gives the team a sense of how the system and subsystems are broken down. At the top of the list is the system itself, the row below are first level subsystems and the following rows.

Car; Chassis; Engine Compartment; Wheel Well; Interior; Steering Wheel Cover; Seats; Carpets; Engine; Transmission; Alternator; Pistons; Drive Train; Wheels; Suspension; Brakes

The second method of modeling the system is the interface block diagram. This model shows the individual components and how they interface with each other, with different colored lines representing different types of interfaces, such as mechanical, electrical, or data interfaces. This diagram helps to solidify how each part ties into the whole design.

System Scheduling; Power; Raspberry Pi; Camera; Motor; Data; Cloud360 Block Diagram Showing Flow of power and data

Keeping a project on schedule is one of the most important systems engineering tasks. When your flight is a set date it is imperative that each part of the design is designed, built and tested by that date. Most issues with payloads stem from poor scheduling, the “art” of pulling an all-nighter the day before the launch being the cause of many untested payloads flying. Given that, a clear, definitive schedule is a great tool for any team.

The best way to display a complex schedule visually is the Gant Chart. A Gant chart lays out each task on the Y axis of a chart and times on the x axis. This is useful for showing how work on each task overlaps with each other, as one subsystem group is working on their subsystem at the same time as another group for maximum efficiency.


i: Example Gant Chart. The Different Colors Represent the different groups working on tasks. Tasks that overlap with each other show tasks that are done at the same time.

System Interfacing
On top of the previous interface block diagram, an interface control document should be made for every system. It can be as simple or complex as needed for the project, but each subsystem needs to know how it will interface with into the main payload to avoid confusion.

This entails listing the electrical connectors or wires needed to connect components, fasteners used to tie a component to the body of the payload, where holes need to be placed for bolts or wires to come through, and even how the software interfaces with the electronics (i.e. pinouts for the flight controller). Setting this stuff early on will avoid confusion and hasty changes down the road.

Product Realization
This section will outline the high-level concepts of Systems Engineering. Product Realization is the act of defining the scope, or defining what is germane to the project, of the project so that throughout the design process, you can check that the payload is still meeting what it needs to do.


Need
The need is the highest-level concept and lays out what purpose the payload is serving. While it seems trivial, it is important that the payload serves a purpose, however small it may be. If the payload doesn’t serve an identifiable purpose, then why should money and time be spent on it?

A Communications payload may be serving the need: “There is a lack of simple, affordable communications devices for HAB projects”
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

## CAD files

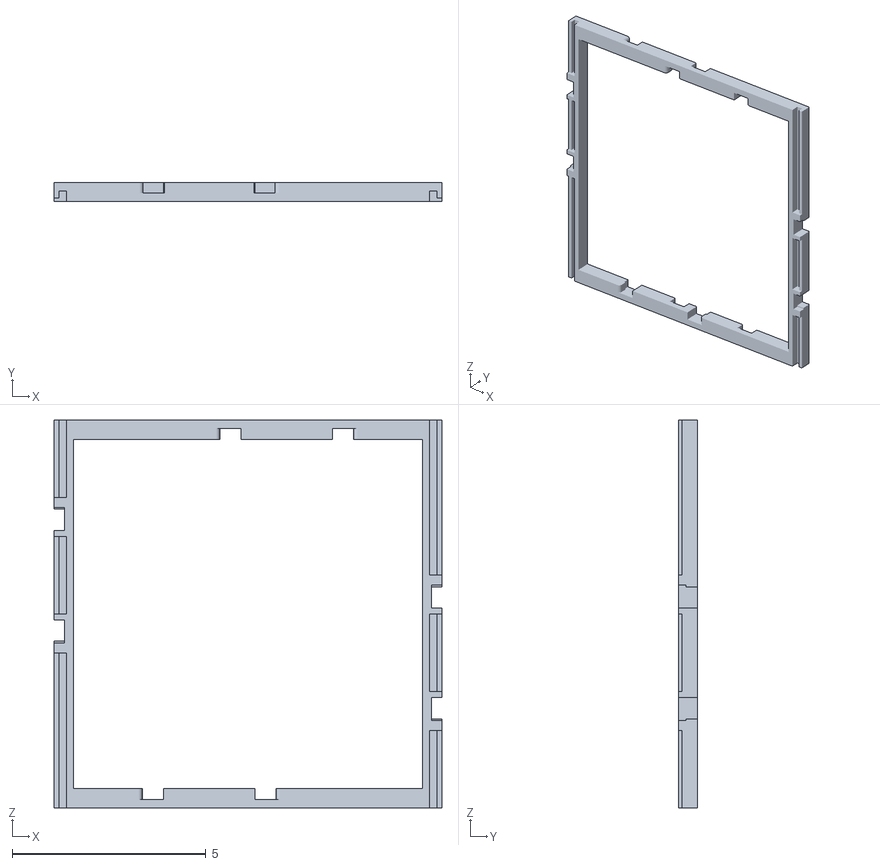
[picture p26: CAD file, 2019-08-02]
PuzzleSat/Female_Final.stl
10.0 x 0.5 x 10.0

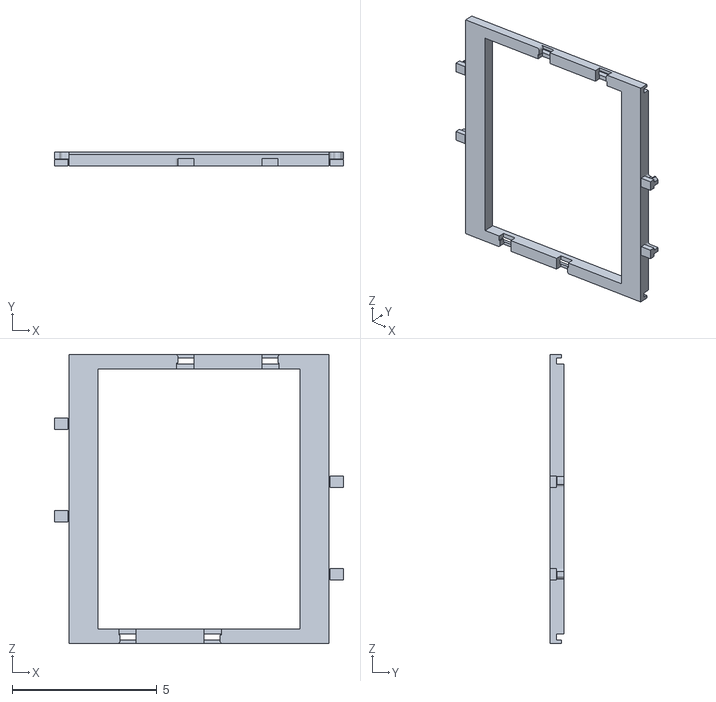
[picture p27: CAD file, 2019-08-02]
PuzzleSat/Male_Final.stl
10.0 x 0.5 x 10.0

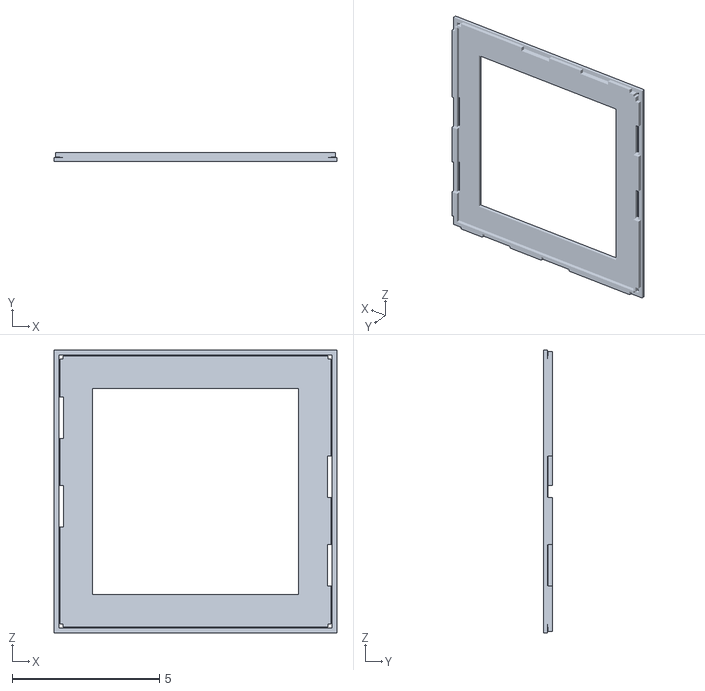
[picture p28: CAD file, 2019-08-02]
PuzzleSat/Slide_Final.stl
9.60 x 0.3 x 9.60

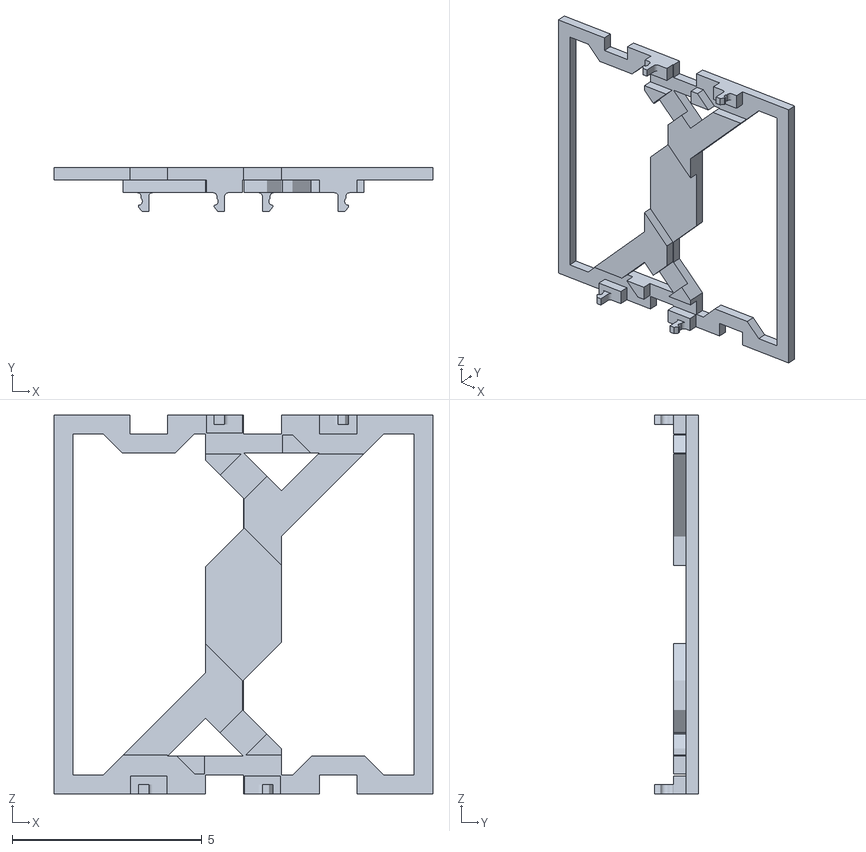
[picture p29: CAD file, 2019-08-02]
PuzzleSat/Puzzle_Connect_Final.stl
10.0 x 1.17 x 10.0

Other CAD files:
CADD_Files/INTERFACE 1.iam
CADD_Files/INTERFACE 2.iam
CADD_Files/PC104 ISA BOARD LOW PROFILE.iam
CADD_Files/PC104 ISA BOARD VERY LOW PROFILE.iam
CADD_Files/PC104 ISA BOARD.iam
CADD_Files/PC104 ISA CUT END.iam
CADD_Files/PC104 ISA CUT INTERFACE 1.iam
CADD_Files/PC104 STACK USB INTERFACE.iam
CADD_Files/PC104 STACK VERY LOW PROFILE.iam
CADD_Files/PC104 STACK.iam
CADD_Files/SOLAR PACKING.iam
PuzzleSat/Female_Final.ipt
PuzzleSat/Male_Final.ipt
PuzzleSat/Puzzle_Connect_Final.ipt
PuzzleSat/Slide_Final.ipt

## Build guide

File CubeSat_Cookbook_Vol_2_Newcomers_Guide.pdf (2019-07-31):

Newcomers Guide to CubeSats, Jorge Rodriguez and others, 2019 | pg. 1

# The Newcomers Guide to CubeSats

### by Jorge Rodriguez and Sandy Antunes

This work is licensed under a Creative Commons Attribution-NonCommercial-ShareAlike 4.0 International License. (https://creativecommons.org/licenses/by-nc-sa/4.0/)

Acknowledgements: The Cactus-1 mission is Capitol Technology University's first CubeSat mission. Our launch opportunity was provided via the NASA CubeSat Launch Initiative. The Cactus-1 mission is supported by grants from the Maryland Space Grant Consortium (MDSGC).

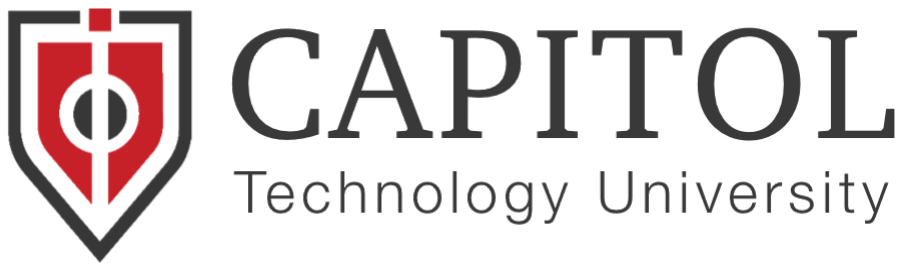
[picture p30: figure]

Specific citations and history are given for each component as follows:
Cactus-1 proposals and mission overviews
A. Antunes, R. Schrenk, R. P. Smith, A. Walters, R. Maharaja, M. Horvath
Hermes payload (on Cactus only-- for Hermes sounding rockets, see Maharaja) by C. Murray, E. Schroen (power Board design), Carlos Del Cid, R. Maharaja, P. Smith, IP rights retained by R. Maharaja
Trapsat payload by R. Schrenk, K. Moore, Z. Richards, M. Strittmatter, A. Walters, R. P. Smith, IP rights retained by R. Schrenk
3U++ Tabbed Frame: by R. P. Smith, R. Schrenk, provided under an open hardware license
Pi-CPU/Health & Safety Boards: by R. P. Smith, A. Antunes, provided under an open hardware license
Power bus: by R. P. Smith, G. Auvray, C. Odigwe, A. Antunes, R. Schrenk
Solar: (Added this because power and solar have different aspects (i.e. licensing to use))
by R. P. Smith with assembly help from George Gieomekis, Marcus Bailey, Sam Lawson, Nick Keller, Sarah Sharpe, Alex English, Nick Aniello, Chris Finch
Passive Magnetics: by E. Routhier, B Reese , R. P. Smith with help by Ian Hastings, Christina Williams
Flight software by A. Antunes with help by Randy Powell, Zalika Dixon, and thanks to Alan Cudmore for useful discussion on his “PiSat” concept
Thermal ets by R. Schrenk with help by Sarah Sharpe, Marcus Bailey, and George Giakoumakis
Comms: by M. Horvath, A. Johnson, A. Antunes
Burn wire, foot switches, inhibits, ports, and subsystems not mentioned: considered either part of the above, part of the general Cactus mission, or not sufficiently novel to merit publication or separate enumeration.
Full list of high-level support (addendum):
Angela Walters, Rishabh Maharaja, Marcel Mabsen, Patrick Stakem, Alan Cudmore, Dave McComas, Suzanne Strege, Alison Evans, Cinnamon Wright
Full list of students (addendum):
Pierce Smith, Ryan Shrenk, Nathan Weideman, Mark Horvath, Alec Johnson, Chris Murray, Sarah Sharpe, George Giakoumakis, Marcus Bailey, Xavier Guzman, Marissa Jagernath, Chukwuma Odigwe, Keegan Moore, Zack Richard, Jamil Ahmed, Gary Visser, Joshua Joseph, Eric Ruthier, Sean Mullin, Christina Williams, Nick Aiello, Randy Powell, Mikus Bormanis, Christel Gesterling, Zalika Dixon, Mike Stritmatter, Josh Hernendez, Ralph Stormer III, Dan Whiteside, Bryce Reese, and others.

uploaded July 2019

Newcomers Guide to CubeSats, Jorge Rodriguez and others, 2019 | pg. 2

## Introduction

by Jorge Rodriguez

Why do you want to build a CubeSat? To photograph space and the earth; to experiment unproven technology and techniques; to create an art project that'll be out of this world? Whatever it is, this book will provide any reader with a baseline platform and information they will need to build a fully functional CubeSat, without jumping through endless hoops to launch the darn thing. This means the designs and instructions are all open source, meant to be accessible and free to anyone, especially DIYers and Students. The years of work have already been done and tested, and we want to release our version to facilitate and shorten the build process for anyone who needs it. Of course, not every project is perfect, and many go through development hell for several years with no end in sight; learning bits and pieces from every key member of the project, CACTUS-1 experienced several hiccups that could have crippled the end product, but the students and professors persevered.

However, the original designeers left room you to play around with; add or remove components, that’s your call. We want this to be as easy as possible, plug and play, however, every build will inevitably have their issues. But the main purpose of the CubeSat Cookbook is to shorten the overall build time, and lesson the headaches that come with designing, coding and assembling a CubeSat. The Capitol Technology University Cactus-1 Team has spent many gruesome years working on Cactus-1, and this book will show the fruits of their labor by contributing their efforts to the small CubeSat community, and help it grow.

## CACTUS-1 Mission

The purpose of CACTUS-1 was to launch two separate payloads in a 10x10x30 cm form factor for about $20k in materials and testing. These two payloads, TrapSat and HERMES, were built by separate teams for different purposes over the course of two years by Capitol students. TrapSat’s main mission was to experiment with a unique material called Aerogel, a low density synthetic porous material in which the liquid component of the material has been replaced by air. While ‘gel’ is in the name, Aerogel is actually a fragile, glass-like material that works wonders as

Newcomers Guide to CubeSats, Jorge Rodriguez and others, 2019 | pg. 3

a thermal insulator and particle capturing device. The latter is CACTUS-1’s intent with Aerogel: to capture space debris and investigate what has been captured using a camera connected to a Raspberry Pi microcomputer that periodically turns on the LED hovering above the Aerogel containment bed and snaps a time-stamped picture of the bed. When radio contact is available, the TrapSat comms team can send a message to the TrapSat to send that data back to earth for the TrapSat team to evaluate the materials flying in LEO. With TrapSat’s mission to capture as much debris as possible, the chosen orbit was a polar orbit (passing above the poles).

CACTUS-1 holds another payload, HERMES: A small attachment to the CACTUS-1 satellite that is completely independent from TrapSat. HERMES is an experimental communications payload using the Iridium Satellite Constellation for uplink and downlink communications. HERMES shares no components with TrapSat other than the chassis they are riding on.

While the build and pending launch of CACTUS-1 is completed, it wasn’t without its problems. Design disagreements, budgeting issues and poor team management were only a handful of key issues throughout the CACTUS-1 campaign as evident by the fact that the original goal for CACTUS-1 was to be ready for deployment in a single year (2016-2017). Of course with such a large project for a small body of students with an even smaller body of volunteers, a viable CubeSat would need the perfect underdog story. We were fortunately to receive an extra 8 months due to launch pushback, long enough for students to gain their bearings, and get to work on a steadier basis, leaving adequate room for learning experiences

Recognize the Spacecraft Subsystems you will need, and consider having a separate team for each. By defining interfaces to meet specifications (such as power and data handling), a large project can be broken into asynchronous small teams, which works well in a university setting.
1. Data processing and handling (CPU and Storage)
2. Communications
3. Attitude control systems
4. Power generation, cleaning and distribution
5. Mechanical
6. Science (Purpose of the satellite)

Newcomers Guide to CubeSats, Jorge Rodriguez and others, 2019 | pg. 4

## Power!

Specifically, battery power! Batteries are everywhere! They power your remotes, smartphones, laptops, and your dusty old gameboy! But as we’ve all come to learn, not all batteries are created equal; Some may remember that joyous feeling when mom came home from The Store and said she got you a brand new box of batteries for you little nintendo. She pulled the unfamiliar box from her bag, and you snatched those suckers out of excitement. You rip out your dying Energizer batteries from the week prior, pop in mom’s shiny new pack of - Dullacell? Of course, you can barely read, but you knew something was off. They didn’t look like the typical Duracell, or the Energizer’s mom usually gets from The Store. But, maybe they’re just alike; after all they’re almost spelled the same. Similar name, same juice you suppose, but heck it all you need to play! You’ve already gotten the weekly rhythm for battery replacement; use your nails for leverage against the positive notch, and - pop! Out with the old, in with the new.

Your daily 8 hour session of Kirby and Motocross Maniacs continues another day! However, you notice that only two hours into your daily grind, the game shuts off and you lose your progress. You sit there angry and confused, and think to yourself “I have new batteries, so what happened?” At the time, none of it made sense, but with foresight, you’ve pointed out the quality. You just had your first experience with poor quality and a lack of heritage, two quintessential properties needed when considering what will power your next CubeSat.

In most picosatellites (small satellites), such as CubeSats, a pack of batteries will power everything from your Pi/Arduino, transceiver, cameras, lights and anything else you throw in your space box. Having a reliable, rechargeable, not-interfering battery is critical to any mission, as this will be the life source of your CubeSat during its flight. Searching for a power source that ticks every box can be daunting, even downright impossible if you don’t know where to start. But that’s what this book is for! At the time of publication (2019), lithium-ion batteries are simply the best, safest option for any amateur space team. Specifically, a good set of 18650 Lithium Ion batteries are well rounded batteries, that has earned its reputation as a reliable source of power for multiple space flights. Knowing the batteries you’ve purchased have successfully not failed in space is one less thing to worry about.

Made from the same stuff as your smartphone and laptop battery, the 18650 Lithium ion battery is a rechargeable battery with space capabilities. From the right manufacturer, these bad

Newcomers Guide to CubeSats, Jorge Rodriguez and others, 2019 | pg. 5

boys can survive both extremes in space, while being recharged by the sun with solar panels . Because of their recharging abilities, 18650 batteries are the go-to choice for many CubeSat enthusiasts. In addition, they are a very dry battery, meaning when they are exposed to extremely high, or low temperatures, the 18650 won’t explode in their case, leaking battery juice in the satellite.

Extreme durability is crucial for flight approval; Your satellite must follow a strict “Do no harm” requirement. Meaning, a CubeSat cannot interfere or damage its neighbors on the launch rocket. This, and many more rules will be elaborated on in the “Requirements and Policies” section. When it comes down to it, there’s nothing stopping your team from using anything else, but to save you time and money, 18650’s would strip the search for power down to brands and your specific power needs.

Finding Batteries

Now, you’ve decided to want to use a pack of lithium ion batteries to power your satellite. Great! If you’re the person of loves a shortage of supplies and hundreds of counterfeits, even better! Unfortunately the 18650 battery market is plagued with liars and lack of batteries themselves. Unfortunately, the search for quality 18650 batteries will require you to be patient and have insider knowledge to get a good deal and avoid fake chinese sellers. This shortage of batteries can be linked to two devices that also use them: Teslas and Vapes. The all electric automotive underdog Tesla packs over 7,000 18650 batteries to power their 85 kWh (Killowatt hour) battery pack for the Tesla Model S. While Tesla has never been on the same production scale as Chevy or Ford, the Tesla lineup has begun to sell like hot cakes in the past few years. Their popularity has caused a significant scarcity of dependable batteries. Trends shape the market, and the surge of vaporizers and quadcopters contribute to the 18650 gold rush as well, meaning manufacturers simply cannot keep up with the demand.

To add insult to injury, many counterfeit sellers take to Ebay to fool any enthusiast looking for their power fix. Fake sellers will take empty shells of a 18650 battery, drop in El Cheapo AA batteries and call it a day, leaving any uninformed customer duped. So when you think you’ve found a great deal from totalllegitseller18298 on Ebay, it’s probably best to shy away. For the best shopping experience, keep to big name brands like Panasonic to supply your battery needs. It’s very unlikely an reputable brand will damage their reputation by selling you a

Newcomers Guide to CubeSats, Jorge Rodriguez and others, 2019 | pg. 6

fake product. Online prices may range from $5 to $17, depending on the vendor. This does not take into account for shipping costs, taxes, and time to ship, so shop wisely!

The number '18650' is simply the dimension of the battery. '18' standing for the diameter of the battery in millimeters, and '650' means the battery is approximately 65 mm long. 18650 batteries are lithium-ion batteries whose charge capacity, charge, discharge characteristics will vary from manufacturer. Held in the spec sheet, is the battery capacity in milliAmp hours (mAh), voltage output, weight, charging specs. In addition, the safe charge, discharge, and storage temperatures in Celsius are given. The graphs show a more detailed look at the numerical values in the above specification. Starting with the charging graph, shows the charging rate at different voltages stopping around 180 minutes. The Life Cycle Characteristics displays the decrease in charging capacity over several hundred cycles. Lastly, discharge characteristics are given by differing temperatures and the rate of discharge.

Battery Box

When you have your pack of batteries, you will need a battery box to neatly use your new batteries. 18650 battery holders are widely available online, varying in quality and purposes. Because most are made with plastic and thin metal connections, getting a hold a holder is relatively easy and cheap. Being straightforward, your main concern will be if you need a series or parallel connection, and the number of batteries held in the box. Quick recap: a holder set in series will increase the output voltage, while a holder connected in parallel will increase the charge capacity (mA). For example, we can use a box that holds four 18650 batteries with a rating of 3.7 V, 3400mAh. If the box comes in parallel, the charge capacity has increased to 13,600 mAh, while a series box will increase the output voltage to 14.8 V. There’s plenty of room to play with in the early stages of your CubeSat, however, your power budget is largely dependant on your weight, purpose, and the components that are using power. Batteries are just a part of the bigger picture, as most CubeSats will rely mostly on solar energy for power, and to charge the batteries during sun exposure.

CACTUS-1 Power board schematic

Presented here is the full schematic of the CACTUS - 1 power board, which proudly displays the battery, voltage regulators, and plugs for the solar panels. Before sending the pcb

Newcomers Guide to CubeSats, Jorge Rodriguez and others, 2019 | pg. 7

files to have this board manufactured, study the schematic to get a full understanding of how current will flow through the board, and where voltage needs to be restricted. On the left hand side of the schematic is a line of solar panel plugs for each panel on the CubeSat. Pierce has also left additional plugs (P5 and P6), in case your satellite may need to attach additional devices. If you are unfamiliar with the busy streets of schematics, please visit https://learn.sparkfun.com/tutorials/how-to-read-a-schematic/overview to get started.

CACTUS-1 PCBS - Sensor, Pi, Solar Autodesk Eagle

The zip file will open with a folder labelled 'PCBs' and an Eagle. epf file, indicating PCB data must be opened with the Eagle program. As the name suggests, PCBs will contain multiple folders and files on the PCB boards for the CACTUS - 1 picosatellite. Opening any labelled folder will reveal a plethora of file versions with a .sch and .brd file extension. Most of these are not human-readable, but assume you are using a PCB editor (like Eagle) or viewer program. A .brd file will show how the PCB board will appear after it has been manufactured. Think of it like the blueprint for a PCB board, which will detail the measurements and how the board schematic is translated to a working PCB. Schematic files end with a .sch extension, and simply show the schematic of the PCB. The other files (.cam, .libr, etc) are support files generated by the program and used by the PCB fabricator.

## Structural Components

Vibration Test Clamp Fixture and Blueprint

Each CubeSat (or any satellite for that matter) must undergo some form of abusive testing to ensure the satellite can survive the trip to space. One form of testing is the vibration test, in which the satellite is put into a chamber, bolted down using a custom clamp fixture made for the satellite, and shaken around to simulate the intense forces felt from a rocket setting out to space. Think of it like the one scene from Finding Nemo where Darla (Braces Girl) shakes Nemo's water bag to high hell; If your dinky space box can survive the frustrated wrath of the metal faced god, you've earned the right to fly.

Newcomers Guide to CubeSats, Jorge Rodriguez and others, 2019 | pg. 8

Bear in the mind the actual vibration motion is much smaller in distance moved-- more like a vibration sander or electric toothbrush-- but a lot faster than Darla can manage, at tens to thousands of vibrations per second. The vibration is run over low and high frequencies based on a spectrum or range, usually using a profile called GEVS (General Environmental Verification Standard, https://standards.nasa.gov/standard/gsfc/gsfc-std-7000) that NASA/GSFC makes available as a default good profile to test with.

Knowing the forces your satellite must survive, it is critical to design and forge a clamp that can secure your CubeSat in place. Provided in our repository is the blueprint used by CACTUS-1 for the CubeSat Vibe (vibration) testing rig. It is based off a design provided by Planetary Systems, modified by Capitol for 3U++ use, and has been provided to Morehead State University so they can test other 'tabbed' designs. A parts list with the part name, size/type, material and vendor is provided, as well assembled and exploded views of the clamp for a better understanding of the product. Additionally, the exact measurements of each component is openly laid out to facilitate the manufacturing process of the test clamp fixture.

CACTUS - 1 3U Tabbed Frame

Pierce Smith designed and drew the metal components for the CACTUS - 1 CubeSat. He designed the blueprint to feature the full dimensions and materials, making it easy for you and your metal manufacturer to replicate the design. Because the CACTUS -1 satellite is technically two payloads, the blueprint presents the framework for both TRAPsat and Hermes. The metal frames for the Bus, TrapSat and Hermes are presented in all their glory in a 1 to 1 scale. Additionally, the design for metal components used to hold the comms board, Aerogel, and batteries are presented.

## Mission Readiness Review (MRR)

From an outsider looking in, the world of space policies, licenses and politics can feel overly complicated (And it is!). Designing and building a satellite can be brutal, even downright heartbreaking when so many things go wrong, or can’t be avoided. But there was a strong

Newcomers Guide to CubeSats, Jorge Rodriguez and others, 2019 | pg. 9

dedication I felt stepping into the Mission Readiness Review (MRR) with the Cactus - 1 team. A devotion to their craft that I have never seen in person, all resonating in one room. Members of TrapSat and Hermes (many couldn’t come due to scheduling) all glowed with confidence and excitement for what they had made. I wasn’t sure what to expect from the review, but I knew I was about to take in much more than I could chew.

MRR and pre-ship are only two of many rviews. Generally you run a PDR (Preliminary Design Review) before you get approval for going ahead with a mission design, and a CDR (Critical Design Review) before they approve going with the final flight build. At Capitol, these are informal, our CubeSat incorporates technology developed in part via our High Altitude Balloon (HAB) launches or in courses. In this context, our PDR is basically 'did a prof look it over and okay it' and CDR is 'are you set up enough that we're willing to buy parts to build it for real', especially with our high altitude balloons. But we did work PDR and CDR into the new Senior Design course, and schedule regular team progress reviews to ensure we were compying with our design docs, goals, and test plans. MRR was the only external review, to both NASA and the launch provider.

What I thought

While reading the NASA MRR checklist, I was left quite anxious and terrified of the events that were about to unfold. I still didn’t know every nook and cranny of CACTUS-1, not the specs, how it was made, or who did what. Yet, here we were in a brightly lit modernist office kitchen, drinking NASA’s coffee, waiting to be reviewed. I had no part in the inception of CACTUS, but the wall of a review still made me incredibly nervous.

Letting my imagination run amok, I expected a grandiose presentation, with the
CACTUS team at the forefront. A stage for the satellite team, men in lab coats probing both man and machine for all its worth. Malicious engineers anxious to pick apart every piece of the team and their slideshow. “Why should we let YOU fools fly?” they would say, seeking to murder a mission. However, what I witnessed was far from my overdramatic daydream; In its place was a friendly hand, nudging and bugging the team towards a successful launch.

Newcomers Guide to CubeSats, Jorge Rodriguez and others, 2019 | pg. 10
What happened

My poor misconception of the MRR ended swiftly, as there was no stage, no lab coats and no maniacal plan for failure. A welcoming breeze from the air conditioned room conjugated with the friendly faces of the reviewer and launch provider, revealing a professionally positive atmosphere for which missions are meant to fly. The room was set in a business-like manner; Professor Sandy Antunes introduced himself as the lead engineer and PI, Pierce Smith and George Giakoumakis represented TrapSat, Mark Horvath from Hermes, and Jorge the writing intern (twas I). Once everyone was formally introduced, the presentation began with Virgin Orbit’s representative (launch provider) giving his power point, detailing the ins and outs of his company’s rocket. Virgin’s presentation primarily detailed their schedule until launch, launch location (California), launch time, actions the payload providers are allowed to do to before departure, and how their payload will be handled before launch. Pressure is put on by both the payload provider (CACTUS-1) and NASA on Virgin Orbit to ensure a safe flight for all payloads; Informing both parties that trained professionals will carefully handle all payloads in a secure location, once the payloads have been received. The launch provider’s MRR is quite short, perhaps 30 minutes of capsulation and integration information. After the launch service presentation is over, the room is open to any questions and concerns.

After all question and concerns were settled, it was our turn to present the CACTUS-1 picosatellite. As the lead engineer, PI, and mentor, Professor Antunes took the lead in the presentation. Beginning the powerpoint with the main mission of both TrapSat and Hermes, he openly stated each payload had separate missions and worked independently, however, shared the same body. Essentially two payloads on one satellite; This lead to rather interesting engineering to work within each space. While discussing the purpose of each payload, the time frame of operation was established for each. Trapsat aimed to achieve their mission within 3 months in orbit. If the spacecraft hasn’t burned up like my late night nuggets, the mission may continue for an additional 9 months. When the 12 months have passed, the satellite must enter a suicide state, manually turning on all LEDs to drain the battery of all charge. Hermes, however, was descoped by our team to operate for a week in orbit, then shut itself down. A licensing issue left the Hermes mission in a rather complicated position, only allowing the use of a specific frequency for 1 week, afterwards the payload must shutdown. Antunes chose to explain the main mission, time frame, any complications or oddities, and how the satellite will terminate itself.

Newcomers Guide to CubeSats, Jorge Rodriguez and others, 2019 | pg. 11

Getting the room up to date with current events on the satellite was next on the priority list. Luckily for CACTUS, Vibe and thermal vacuum testing was completed just one week prior to the MRR, giving the team a chance to focus on the final build. A majority of the MRR was discussing the many quirks and features of the satellite, such as preliminary actions to prevent the antennas from deploying early or powering on during launch. In the case for TrapSat, a burn wire is set in place to deploy the antennas once in orbit; Hermes uses a timer prior to launch to prevent accidental power and voiding their license.

Overarcing issues such as Environmental Requirements that must be met with a CubeSat to be Environmentally Compliant are mostly handled prior to the review in the ODAR (Orbital Debris and Re-entry) filing we had to make with the launch brokers. Basically, we list all our materials in case any might be a problem. Other than that, we don't have much because we're not firing rockets. The rocket company has a lot of this paperwork to do for their rocket, though.

“Deployables verification” simply mean to explain that the satellite has deployable equipment attached, and that its purpose and that it conforms to any size/weight/safety requirements set in place. The other verification is providing evidence you tested it. We have 1 deployable on Cactus-1-- the antenna. A burn wire burns and the tape-measure antenna springs out from where it's tied to the side of the satellite. So we have to state that yes, we've tested the burn wire system and it works, and also that (safety requirement) we are confident that it won't deploy early or accidentally and thus cause a risk to the rocket.

The main discussions answer many general concerns, like potentially hazardous materials that flying aboard. “How will they be shielded within the CubeSat to prevent exposure to the rocket and surrounding payloads?” “Will your team need to apply for any waivers to approve the fit your size budget?” “What about any major problems and concerns you encountered during your build time or brought up in Vibe?” These are only a fraction of the questions you will encounter during the MRR to ensure a safe flight, not only for your team, but for every payload sharing the same launch rocket.

When discussing “Mission Assurance Issues” to the board of reviewers, common topics are there to discuss regarding the team’s confidence in their mission. Our MRR team covered this when we went, a lot of that meeting/MRR was them bringing up questions to make sure we are set. One required item is “System Verification update and non-compliances”, which is a

Newcomers Guide to CubeSats, Jorge Rodriguez and others, 2019 | pg. 12

catch-all to bring the review board up to date on any compliance concerns so it can be evaluated and either given a timescale to bring into compliance, or lead to a waiver being filed.

However, it cannot be emphasized enough to read through the PRP (Preferred Reliability Practices) MRR packet to double, triple check each bullet to make sure your mission fits within their specs. The MRR isn’t a scary test meant to scare the weak. NASA wants you to pass just as much as you want to see yourself pass. In end, it’s meant to see what your build and mission may be lacking, and how your team can improve before the launch date. Whether it’s to finish the build, get tested, or trivial glitches, get it done after this progress review, and good luck.

Newcomers Guide to CubeSats, Jorge Rodriguez and others, 2019 | pg. 13

## How to improve team management and keep team members

gathered by Jorge Rodriguez from interviews with the Cactus-1 team

Cactus-1 was a student-led student-run mission where professors played a minimal role in oversight, primarily providing mentoring support and procurement support. As such, we noticed some general rules and tips from our build, that involved 30 students over a 3-year span.

TrapSat Mission
- “TrapSat is a debris collection, imaging, and profiling subsystem with the goal to map out debris clouds in orbit.”
Hermes Mission
- “Hermes is an experimental payload communication payload using the Iridium constellation for uplink and downlink communications.”
Why they use their orbit?
- “The chosen orbit was a polar oribit (Altitude disclosed driven maily by TrapSat’s desire to collide with debris which is common at the poles.”
Planned Lifetime
- “About 3 months, with extended missions possible as far as the space craft survives.”

Budget
- Goal: budget of about $20k, while the end cost of the satellite was under $10k

Working as a student and teacher relationship
- A relationship is still a relationship as both parties getting back what their putting in?
- Keeping and organized system of notes of the project is essential so information isnt lost to the void (Pierce solved most of this with his senior project)
The management

Newcomers Guide to CubeSats, Jorge Rodriguez and others, 2019 | pg. 14
- Prepare for the meetings/ establish a fixed time for weekly meetings
- Bring results, questions and an agenda to your weekly meetings
- Make weekly progress
- Keep everyone posted to keep communication across the team

Working with others
- Be clairvoyant with your team
- Detail what has/ hasn’t been done
- What you need help with
- What you don’t understand

Pick a topic of mutual interest
- Begin with something in common for the beginning of the relationship
- (Personal Note) For me it was the interest in cubesats and space physics/ satellites/ NASA
- Have students build an emotional time for the project? (Not easy or forced but inspiration for students not to quit?)
Be explicit about what you need from your advisor
- Advisor will always be a compromise between their personality, your personality, his advising philosophy and the realities of limited time
- Ask for more guidance of a different way of guidance
- Your value to the project lies in how much you get done it doesn’t matter whether you invented it all yourself
Be a team player
- If there are other people in the project, find out what they’re doing
- Ask questions
- Get a broader sense of the project beyond your part of the project

Share what you do
- Back up your work

Newcomers Guide to CubeSats, Jorge Rodriguez and others, 2019 | pg. 15
- Comment your code
- Log experiments
- Keep everything valuable in a shared repository for yourself, your advisor and other teammates to look back on and study
- Use github, google drive, dropbox
- BUT KEEP IT CONSISTENTLY IN ONE PLACE

Avoid diffusion
- Do not spread out work over many different repositories, cloud services, emails , making it hard for anyone to look back and create reports for simple checking
- Keep track of what you’ve done as simple notes

Why do team members leave?
- frustration began from starting from scratch
- Short time and small budget was a restraint
- Began as a large collaborative effort from several departments of capitol
- Not enough consistent hands on board

Pierce Interview Notes
- Pierce noted that there was a disconnect between people in the subsystem level and whole level
- Real world there’s going to be a disconnect
- You get paid and you’re done
- This isn’t the real world, so there should have been more communication in the team
- A lot of frustration with heritage
- Originally had a powerbarod research team

Newcomers Guide to CubeSats, Jorge Rodriguez and others, 2019 | pg. 16
- The team wanted a powerboard build by another team that had been used and worked
- Good example of heritage (According to Pierce)
- Could not find information on the board from the team that built it
- Powerboard team could’t find reliable information on a powerboard that had been previously used
- They insisted on creating a new board but was shut down because higher ups insisted on boards with heritage to appease MRR.
- Powerboard team quit because they weren’t allowed to build anything
- This point was made even more clear because the powerboard chosen, was then redesigned had barely been questioned during the MRR, and because it had been overlooked, it goes to show that heritage is not the end all be all of a project
- Quite a bit of advice and concerns from other professors and students were ignored when reviewing certain boards
- A lot of time was used to soldering and wiring high efficient solar panels, essentially wasting valuable time and manpower for minimal gains
- Time could have been saved with bigger, less efficient boards
- Comms board team could not figure out how to fully utilized the comms board because of how undocumented it was.
- When choosing outside built equipment, make sure it’s fully documented or built in house so that it does not take months to understand an essential piece of equipment
Pierce Tips
- Ease of assembly
- Documentation
- Has it been flown before? / heritage
- Price
- PC 104 electrical and physical standard boards (only used physical)

Newcomers Guide to CubeSats, Jorge Rodriguez and others, 2019 | pg. 17

Beginning People
- Started out with about 50-60 people (According to Pierce)
- Many of whom were just lurkers
- Many people stayed to simply help, like hold wires, assemble boards and generally being a helping hand
- Spreading out the workforce to simply helpers, developers and designers could alleviate the stressful development of CubeSat
- Designated helpers

## Lessons Learned

Here we go through many of the lessons learned after our 3 year build. In Appendix A and Appendix B, we reference our Cactus-1 build explicitly, while in this section we cover general design and team management choices that would be of benefit to any team starting on a CubeSat project.

Successful ‘Final Push efforts’ by hard working students to complete milestone

λ Final few dedicated students performed excellent work when approaching internal deadlines
λ Final push efforts happen a lot because students are very busy while school, work and life

λ Find reliable and hardworking students that want to stick around to make a successful mission
Adaptation of designs and future-proofing work helped keep the program and keep schedule slip to a minimum
λ Implement future proofing to designs

Newcomers Guide to CubeSats, Jorge Rodriguez and others, 2019 | pg. 18

When two configurations are considered but unsure, implement bot so that future teams may choose either config in their designs
λ Future proofing saves time and money for future development

λ CubeSats are difficult for waterfall style work because new discovery of work tends to happen and future proofing may alleviate the unknown problems early on

λ Design Choices involving heritage were not properly analyzed

λ CubeSats meant to be experimental, not many CubeSats will have heritage

λ It is important that a team challenges a heritage idea that the same way it would challenge any other idea
λ A good idea, decent design, decent testing and documents to back t up will be more than enough to fly

Fixation on heritage

λ Choosing to rely so heavily on the heritage power board was thought to be a good idea for legitimacy, and ease of use.
But new or old, the design didn’t matter and there was so many mods done to the board that in retrospect a new board would have been better.
λ Using the knowledge from the mission Pierce suggests to create a new powerboard for the next capitol mission.
Or create specific criteria for an existing board to minimize modification.

■ Want to create a One-size-fits-all design for CubeSats

λ Cookbook Vol 1, Pages 29, advice and assumptions, are very important to your next design
λ The assumptions about budget and size only apply if your design is similar to Pierce’s

λ It was no repeated many time sbut heritage is not the end all be all

Newcomers Guide to CubeSats, Jorge Rodriguez and others, 2019 | pg. 19
Designing

λ When designing in house, it can be an excellent learning experience for students to learn the ins and outs of a system
These rules don’t really apply to processors and comms equipment as it would costs too much time and money to develop
Keep an eye on the power budget of the systems

■ Systems/ Comms ops Page 30

λ Systems Synthesis = System Design

Translate the system functional architecture into a physical architecture.

■ It creates a “how” for every “what” and how well.

λ This design can be seen by how you would want to move while in space
Completely passive

Minimal pointing with magnets PMAC

3 point axis controls with React Wheels

λ PC /104 PCB Standard suggested many times

Newcomers Guide to CubeSats, Jorge Rodriguez and others, 2019 | pg. 20

## Appendix A: A Short List of Cactus-1 Considerations

This is a list of Cactus-1 subsystems and operations needed. Cactus-1's detailed engineering specification are provided in “Cookbook Vol. 1”. We provide this list here to provide new teams a look at the number of potential subsystems so as to help you with forming appropriate teams to tackle the project.

λ Comms
λ | Comm board
λ | Antenna
λ | CPU (Pi)
λ | Health and Safety Sensors
λ | Temperature
λ | Accelerometer
λ | Magnetic Field
λ | Battery/power levels
λ | etc

λ
λ Structure
λ | 3U metal frame
λ | footswitches and inhibits
λ | pointing/attitude
λ | Passive magnets + hysterisis rods
λ | Burn wire for antenna deployment
λ | Thermal ets/mylar

λ

Newcomers Guide to CubeSats, Jorge Rodriguez and others, 2019 | pg. 21

λ Integration and Testing (I&T)
λ | Integration
λ | anti-static
λ | wiring
λ | mounting stuff
λ | software
λ | Testing
λ | component testing
λ | Shake & Bake (vibe test, thermal vacuum test)

λ
λ Payloads
λ | TrapSat
λ | chunk of aerogel
λ | 2 cameras + LEDs for lighting
λ | triggered by CPU, sends back images
λ | Hermes
λ | COTS Iridium satellite modem
λ | stand-alone; has own power etc

λ
λ Licensing and Policy stuff
λ | MRR-- Mission Readiness Review (must-pass 2-hour review by rocket people)
λ | FCC paperwork (and IARU/ITU stuff)
λ | NOAA (approval for cameras)
λ | Policies
λ "Do No Harm"
λ | Heritage
λ | OS and COTS vs Custom design
λ | Limits: 1.2kg/U, each U is 10cm x 10cm x 10cm, we're a 3U

Newcomers Guide to CubeSats, Jorge Rodriguez and others, 2019 | pg. 22
λ | Requirements?

λ
λ Ground Station
λ | Antenna
λ | Radio
λ | Software
λ | ConOps (Concept of Operations)

We also provide our candid look at our initial plan and schedule, what constraints drove that, and how this matched the actual build process as it unfolded.
Cactus-1 Constraints
- Many risks and constraints
- small school with small budget
- schedule, cost and scope
- To be built under $20,000 and in 2 years
- Because of the small cubesat community, pre-built subsystems were very expensive ($5,000-10,000 average) and finding subsystems that fit specific needs also difficult
- Because of this, subsystems had to be developed in house to satisfy their needs and fit with the budget
- Outcomes
- Succeeded in budget goals
- figure 3 shows $9,300 on just CubeSat
- Figure 4 shows $17,150 for whole program (out of $20k)

Time and Schedule
- Development started in August 2016 with goal to complete in August 2017
- Much of the project was rushed and nowhere near completion by following year
- Many risks that come with amateur CubeSat increase R&D time

Newcomers Guide to CubeSats, Jorge Rodriguez and others, 2019 | pg. 23
- Lack of knowledge
- Need for flexible time schedules
- Decrease in class participation
- Lack of knowledge
- Led by sophomores
- Students had some experience with other sounding rockets, but wasn’t enough to prepare the CubeSat workload
- Many students first project
- Large hassle as students needed to teach other students, rather than work on the project
- Subsystems had many mistakes
- Need for flexible time schedules
- Many mistakes meant for schedules must compensate for amateur mistakes
- No Subsystems defined from beginning so development was in series, not parallel ideally
- Decrease in class participation
- Lost interest, felt unneeded or stopped by school work
- Development on several subsystems halted and need to be picked up sequentially by remaining students
Scope
- Two goals for cactus-1 made it rushed
- Built in one year and under $20k
- Already a big project, then added difficulty of 2 goals
- Cactus-1 would have been unachievable from the start if it weren't for launch schedule slips
- Capitol has a reputation for building well built systems on a very low budget

Newcomers Guide to CubeSats, Jorge Rodriguez and others, 2019 | pg. 24
- Niche commercially available parts were too expensive for initials goal, thus 'buy or build’ was relegated to 'build’ while delivering a fully functional system

Design Choices

Attitude control system
- Basic requirement is to keep in line with velocity vector and enable communications when needed
- Low cost, low complexity, SWaP properties
- Chose subsystem called Passive Magnetic Attitude Control (PMAC)
- No input power
- Low space + low mass
- No commanding (passive)
- Simple to operate, hard to implement
- Uses hysteresis rods
- Must use simulators to know right amount of hysteresis for how strong magnet should be
- System should be accepted but would flip 180° when going over poles
- Cheap enough to work but now the TrapSat Payload needs to be mounted on both sides for access
Power systems
- Power subsystems was open ended
- Needs to provide power to Raspberry Pi and comms system
- Follow PC 104 standard
- Physical required
- Electrical preferred (Discussed later in doc)
- Could buy, buy from University, or build in-house

Newcomers Guide to CubeSats, Jorge Rodriguez and others, 2019 | pg. 25
- Buy too expensive
- University parts were sadly undocumented so very unhelpful
- Logical choice was to build in-house
- Original powerboard came from Interorbital CubeSat for free
- Comms system from same company so integration theoretically easier
- Not used because lack of sufficient voltage and lack of documentation
- Power board drastically modified to make it reliable
- Powered by 18650 batteries
- Cheap logical choice

Mechanical and Physical
- Biggest constraints for system, for deployment, and launch provider
- Vibrational, physical size, and surface characteristics
- Structure big priority because most expensive and longest turnaround time
- Used commercially available frames as reference and inspiration for custom design to avoid buying
- If cost of buying vs building were similar, it would have been more logical to simply buy a frame
- Planetary Systems inspired the single part to meet the mating requirements of tabbed sked interface between launcher and CubeSat
- Vibrational and physical requirements go to rest of structure and allow for tolerances
- TrapSat payload need to be facing velocity vector during orbit to trap debris
- Payload on front and back of CubeSat
- HERMES on the bottom end
- Have to find a right balance in payloads and components to balance center of gravity

Newcomers Guide to CubeSats, Jorge Rodriguez and others, 2019 | pg. 26

Hermes Physical Segment
- Card Stack
- Batteries
- Shell
- Solar Panels
- What is a helix antenna?
- Look at Cad files of Hermes to have understand its components

Thermals
- Thermals (Something to generate heat) not considered because temperature fluctuates between -10 Celsius and 10 Celsius
- Mylar eting and hybrid aerogel insulation to insulate the CubeSat
- eting used inside and out to reflect sunlight, insulate the cubesat and because it is conductive

Solar Design
- Need to know basic electronics
- Voltages
- amps
- whiskering
- types of solder
- silicon sealant
- circuitry mitagation
- diodes
- etc.

Newcomers Guide to CubeSats, Jorge Rodriguez and others, 2019 | pg. 27
- Learning basic electronics is key to designing efficient solar panel integration and placement

Manufacturing
- Decide on who makes PCBs
- Make PCB files yourself in Eagle
- Free software good enough for the job
- Have a professional create the PCB
- Can learn how to read and design PCBs by following Pierce
- Pierce provides a short tutorial on how to recreate his solar panels in this final doc

Noted Efficiencies
- Packing efficiency
- How much you can mathematically stuff on a surface
- Solar power efficiency
- High efficient solar panels offset the low packing efficiency meaning they cannot reach peak potential
- Lessons learned
- Learned from the geometry of the solar cells and solar panels to improve the rigidity of each cells in its uncut form
- A lot of wasted space between the cells
- Reduced work and time by opting for larger solar cells/panels
- Efficiency loss using larger cells (50% eff) offset by larger area (2x area) plus adds ease of assembly.

Power Design
- Power comes in, cleaned and goes to charge or goes directly to power the system

Newcomers Guide to CubeSats, Jorge Rodriguez and others, 2019 | pg. 28
- Students need to study how powerboard PCBs function
- Parallel and series circuits
- Students need to learn about voltage regulators
- Voltages for your needs and reliable voltage
- Voltage regulator does all the work

Power Distribution
- Charged from the original design
- This was changed because original board was very unreliable and provided weird voltage
- Removed boost circuit to DC DC converter
- Need to know what these are.
- What are trim resistors in a circuit?
- Need to know when to quit with certain equipment to avoid frustration and no progress
- What is lockout voltage?
- Lowest voltage something can function at, when below this voltage deville will turn off
- What is a Linear regulator?
- Incoming voltage from the solar panel will be converted to lower bus voltage
- Deciding trade offs with efficiencies
- read page 26
- Do you know how to add filters to a circuit?
- Protection diodes are useful

Newcomers Guide to CubeSats, Jorge Rodriguez and others, 2019 | pg. 29

## Appendix B: Markup and Comments on Capitol CubeSat Cookbook Vol 1. (the Engineering Guide)

We provide 2 sections here. First, a rating/review of our CubeSat Cookbook Vol 1.: The Engineering Guide, indicating the technical level of each section. That is followed by specific design insight and lessons learned to accompany that book. Note the table below also acts as a preview for the Vol. 1 Table of Contents, and we recommend you download this book as well!

Cookbook Vol. 1. Engineering Document Technical Difficulty Rating
CACTUS-I Overview . | 5 (Easy)
CACTUS-I System Design | 6 (Easy - Intermediate)
Constraints | 6 (Easy)
Time and Schedule | 7 (Easy)
Scope | 8 (Easy)
Design Choices | 8 (Intermediate)
Attitude control system | 8 (Intermediate)
Power systems | 9 (Intermediate)
Mechanical and Physical | 9 (Intermediate)
Lessons Learned | 11 (Intermediate)
What Went Well | 11 (Easy)
What Did Not go Well | 12 (Easy)
CACTUS-I Structure Design | 13 (Easy - Difficult)
Major Design Features | 13 (Intermediate)
Overview of Interfaces with Launch Provider | 14 (Intermediate)
Material Choices | 15 (Difficult)
BUS Segment | 15 (Intermediate)
TRAPSat Segment | 16 (Easy)
HERMES Segment | 16 (Easy)
Thermal | 16 (Easy)
Vacuum | 17 (Easy)
Lessons Learned | 17 (Intermediate)
CACTUS-I Solar Design | 18 (Easy - Difficult)
Interfaces and Connections between Segments | 42 (Difficult)
Solar | 45 (Intermediate)
Larger Solar Cells | 45 (Intermediate)
Larger Solar PCBs | 49 (Intermediate)
The Fallback, using the Same Cells | 50 (Intermediate)
Electrical | 50 (Easy - Difficult)
Interfaces and Connections between Segments | 42 (Difficult)
Solar | 45 (Intermediate)
Larger Solar Cells | 45 (Intermediate)
Larger Solar PCBs | 49 (Intermediate)
The Fallback, using the Same Cells | 50 (Intermediate)
Electrical | 50 (Easy - Difficult)
Special note | 50 (Easy)

Newcomers Guide to CubeSats, Jorge Rodriguez and others, 2019 | pg. 30
PC/104 ISA | 51 (Difficult)
Power Conversion Methods and Applications | 53 (Difficult)
Bus Voltage | 60 (Difficult)
Special note | 50 (Easy)
Interfaces and Connections between Segments | 42 (Difficult)
Solar | 45 (Intermediate)
Larger Solar Cells | 45 (Intermediate)
Larger Solar PCBs | 49 (Intermediate)
The Fallback, using the Same Cells | 50 (Intermediate)
Electrical | 50 (Easy - Difficult)
Special note | 50 (Easy)
PC/104 ISA | 51 (Difficult)
Power Conversion Methods and Applications | 53 (Difficult)
Bus Voltage | 60 (Difficult)
PC/104 ISA | 51 (Difficult)
Power Conversion Methods and Applications | 53 (Difficult)
Bus Voltage | 60 (Difficult)
Materials | 18 (Intermediate)
Direction on Manufacturing | 19 (Difficult)
Efficiencies | 21 (Intermediate)
Lessons Learned | 21 (Easy)
CACTUS-I Power Design | 22 (Easy - Difficult)
Design Overview | 22 (Easy)
Power Input and Cleaning | 24 (Intermediate)
Charging | 25 (Intermediate)
Power Distribution | 25 (Intermediate)
Lessons Learned | 26 (Intermediate)
Future Guidance | 28 (Easy - Difficult)
Assumptions . | 28 (Easy)
Advice | 29 (Easy)
Recommendations for Design | 29 (Easy)
Systems | 30 (Easy - Difficult)
Con ops | 30 (Easy)
General design constraints | 30 (Intermediate)
Systems Synthesis | 30 (Difficult)
Interfaces | 33 (Difficult)
Power budgeting | 37 (Intermediate)
Mechanical | 38 (Easy - Difficult)
End Mount Improvements | 38 (Easy)
Card Stack Improvements | 38 (Difficult)
Tabbed Sled and Shell Improvement | 42 (Difficult)
Interfaces and Connections between Segments | 42 (Difficult)
Solar | 45 (Intermediate)
Larger Solar Cells | 45 (Intermediate)
Larger Solar PCBs | 49 (Intermediate)
The Fallback, using the Same Cells | 50 (Intermediate)
Electrical | 50 (Easy - Difficult)
Special note | 50 (Easy)
PC/104 ISA | 51 (Difficult)
Power Conversion Methods and Applications | 53 (Difficult)
Bus Voltage | 60 (Difficult)

Newcomers Guide to CubeSats, Jorge Rodriguez and others, 2019 | pg. 31

## Cactus-1 Specific Engineering Design Lessons Learned

1. Making a new CPU would be too risky and costly for a small school, but using an existing CPU like an arduino or Raspberry Pi
1. Check Page 33 for questions for each subsystem
- Look through Texas Instruments tech files for circuit board power supplies because Texas Instruments provides very detailed information on creating your own power supply. As stated by Pierce TC provides detailed information on how integrated circuits work, common circuits created with IC and the math behind it all.
- Because the mechanicals for Cactus-1 worked well, Pierce recommends to use the mechanical as a base for new systems
- Akins 15th law of Spacecraft design
- Design structure matrix (DSM) called N^2, is a matrix used to examine the interferees of a proposed system design
- Make a simplified design interface to avoid complication as the build itself will be heavily complex
- Understanding DSMS can be hard for the uninitiated
- Cubesats are meant to be looser paths to success than high scale, expensive satellites as much of the design comes from new experiences and exploration from students
- It is still recommended to use ISA PC 104 physical standard,
- while the electrical standard could have been used, the board required would add unnecessary complexity to the board
- The board was specialized for this mission

Power Budgeting
- A power budget is the balance between power coming in and power going out

Newcomers Guide to CubeSats, Jorge Rodriguez and others, 2019 | pg. 32

Mechanicals (Cookbook Vol 1, page 38)
- The sled launching design worked well so this design should be used again for CACTUS -II or the CubeSat you make
- Other launch designs considered but this works well
- (Cookbook Vol 1, page 38 and 39)
- Card stack improvements are very technical
- Leave to students to figure out

Interface 1
- Technical heavy to improve stack design

Interface 2
- Improvements or adjustments to the card stack design that may function for your design
- Omitting some components for others etc.
- Technical heavy

Solar (Cookbook Vol 1, page 45)
- High packing efficiency > low packing efficiency out balances low efficiency large cells
- if these powers balance out then that would mean a reduction in time and money for the same power output.
- When comparing solar panels, consider its length, width, max voltage, max current, power output per unit, wattage per area, price, price break and price per milliwatt
- Attempting to improve packing efficiencies
- By using the same boards and cells, packing efficiencies could be improved in software by packing the cells in s a geometrically efficient way without thinking about human error. But real world examples would be very difficult task for students as they cannot recreate perfect computer designed boards.

Newcomers Guide to CubeSats, Jorge Rodriguez and others, 2019 | pg. 33
- Compares various solar cells from IXYS which are 22% efficient and packing efficiency tends to be 70%
- Smallest size available from IXYS that generates .5 Volts and 44.6 mA. These need to be connected in series to have a useable voltage
- IXYS also offers multicell devices such as this 9 cell device which connects the small cells in series for convenience
- A comparison list is very handy for comparing size, power and power between solar cell units to determine the best cell for your needs and budget
- Such as the Trisol X single cell vs IXYS single cell: $2 vs $1.4; 2.3V vs .5V; 14.6 ma vs 44.6 mA; etc.
- Pierce discusses the values of efficiency (lower = better)
- Trisol X 28% while IXYS only 22%
- Connection methods, time to build, quantity available, and ease of implementation should be considered
- Pierce compares the large SLMP121Ho9L 9 cell IXYS to the existing Trisol X had built solar panel design
- Mid range wattage per one and price per wattage
- Larger panel = shorter time to build
- As of now (2019) plenty of parts available for CubeSat build
- Based on previous experience, this board could be easier to work with since it uses the edge solder method
- not large, implementation easier into PCB
- Max voltage output is 4.5 volts, which is ideal for low voltage bus using 18650’s

(Cookbook, page 48)
- Pierce redesigned the original solar panel to use the 9 cell IXYS cell and found that even from an individual power cell efficiency may drop from 28% to 22%, the packing efficiency has doubled, bringing an additional 20% over power: 510 mW (Trisol X) to 602 mW (IXYS)
Larger Solar PCB’s (Cookbook Vol 1, page 49)

Newcomers Guide to CubeSats, Jorge Rodriguez and others, 2019 | pg. 34
- Pierce noted that the way Cactus is built means that segments of the build could be taken and used as its own thing for other projects, however, because each satellite is unique, this perceived benefits is actually not useful. Because the modular feature is not needed the solar panels attached to the shells can be bigger based on pierces original design to span across multiple shells. This theoretical design could still work with the tabbed sled and solar panels.
- Pierce showcases the small and large solar panels he designed in EAGLE.
- Because of the limitations of the free version, he could not create a merged board because of the area limitations
- This can be remedied by paying the monthly/ yearly subscription
- If given access to the paid version, Pierce could have merged 3 boards together for an increase from 55% to 58% in solar area, without creating 2 separate boards with wasted space in between
- A 9.25% increase in performance would be seen as a merged board would allow for 5 extra cells

The Fallback, using the same cells Page 50
- Pierce desperately wants new cells to be used, however, if the Trisol X cells must be used, the packing efficiency has to be improved in the next generation to add new cells
- Tips for new board
- Corner of cells re added to fall into position easier
- less soldier paste used for each cell
- packing efficiency increased by placing solar panels closer together
- To determine how close, students must learn to build a board and begin to plan the layout by their experience
- Pierce provides a software example (Figure 43) to show what a new board could look like if assembled perfectly to improve efficiency and add additional cells. though tight, it can be done with steady mind and steadier hands.

Electrical

Newcomers Guide to CubeSats, Jorge Rodriguez and others, 2019 | pg. 35
- Pierce highly suggests the power subsystem be build in-house for better integration and because it is the easier of the subsystems to create from scratch.
- Wants to new subsystem to be PC/ 104 compliant for easier wiring
- 3 Sections
- Solar input and cleaning
- power storage, charging and discharging
- Power distribution and conditioning

Special Note
- Pierce leaves power board design to Erik Schroen. He has more experience with power board designs -- see his work in our Cookbook Vol. 3!

Power System Block diagrams and controls Intermediate Difficulty Technical
PC/ 104 ISA
- Board stacking design to PC 104 board
- Female boards on top .1” spaced apart and male pins on bottom to stack boards with pins indefinitely
- Pins available from SAMTEC
- Can be purchased from Maser Electronics
- 32 x 2 pin and 20 x 2 pin header
- ESQ-132-14-G-D
- ESQ-120-14-G-D
- To save space, remove the break away spacers on the header, which measures about .435”
- Or order headers without spacers

Newcomers Guide to CubeSats, Jorge Rodriguez and others, 2019 | pg. 36
- The benefit of standardizing the boards evident as Pierce demonstrates that the interconnected board layout constructs power pins that can provide power to every device connected to the pin.
- Total pins available 104 (2 x 32 + 2 x 20)
- If needed, J2 (2 x 20) can be larger to provide additional pin, but would break ISA interface standard
- ISA interference can only provide 1 amp per pin
- If more amps are needed, use 2 pins and a 10 Ohm resistor to balance current
- A wiring chart will be necessary to manage any connections with wires
- Create pin chart of the ISA pin layout

Power conversion methods and applications Page 53
- Linear Regulators
- Boost Converters
- Buck Converters
- DC DC COTS
- Power storage with batteries

Linear Regulators
- Brings high voltages down to low voltages
- Done by shunting excess current to ground through another component link
- Efficiency varies depending on voltage difference from source to target voltage
- Greater the difference, more voltage sent to ground, the hotter they get
- Does not use switching frequency to raise or lower voltage
- DC voltage is fairly consistent
- Can react quickly to a charge in source voltage

Newcomers Guide to CubeSats, Jorge Rodriguez and others, 2019 | pg. 37
- output voltage not interrupted by change in voltage
- not useful for capitol grade CubeSat but it is nice to have
- Power wasted from linear regulator
- P = (V in - V out) * I Load
- Efficiency dependent on voltage difference
- Efficiency = ((V in - V out)/(V in)) * 100

Pros and Cons
- Not efficient
- Cheap
- Very low noise input
- wasteful for power-starving CubeSats

Boost Converters
- Called a Switch Mode Power Supply
- Generate high voltage outputs from low voltage inputs
- Uses high frequency switching in combination with inductors, capacitors and diodes to create hight, steady voltage
- See figure 47 for Boost Converters explanation
- Active switch will turn on and off at high frequencies
- two stages to consider for the boost circuit
- Assume two things
- In Continuous Conduction Mode (CCM)
- Already reached Steady State (SS)
- CCM means current in conductor will never reach zero

Newcomers Guide to CubeSats, Jorge Rodriguez and others, 2019 | pg. 38
- Indicates circuit already providing expected power board

Good applications for these devices (Assuming voltage bus 3.6v to 4.2 volts)
- Communications high voltage source
- DC DC converter followed by LDO linear regulator for high voltage, low noise
- General 5 V power source
- boost converters for efficient 5V power source
- Solar Input
- Because each case is different, you may find that a buck converter, linear regulator or a circuit is necessary for the voltage needed by the Bus.

Bus Voltage Page 60
- Central voltage that power distribution will run from
- (Solar) input voltage converted to bus voltage; converted to acceptable voltage for power distribution
- Part selection and cost may revolve around bus voltage
- Pierce mentions that an unregulated bus voltage is just a raw power source whose voltage may vary
- this can be seen if the battery were connected directly in the CubeSat, meaning the battery was the bus voltage
- Solar power is similar
- battery charging occurs during sunlight - regulated
- When not charging battery sends power directly and is the bus voltage -unregulated
- Because of the variability of voltgages, the circuitry needs to be able to handle the expected voltage ins
- Pierce clearly designed a circuit board that would try to provide a steady voltage between 3.4 and 4.2 volts

Newcomers Guide to CubeSats, Jorge Rodriguez and others, 2019 | pg. 39
- Battery voltage varies from 3.4 to 4.2 volts depending on charge
- Solar input of 4.2 volts to allow charging at any point
- When detects battery below 4.2 volts, will provide solar current to battery
- Because of the varying voltage, all power distribution outputs must be able to take in 3.6 - 4.2 v and convert it to the necessary voltage for each subsystem
- Pierce’s power system is dynamic enough to distribute power to multiple subsystems with a clean voltage, and can be slightly modified with additional batteries in series to provide a higher voltage; A higher Bus voltage provides a wider range of potential voltages and alleviates stress on the components by lowering necessary current flow. Because of its background, the power bus may dynamically send power to any component at any time, dark or shine.
- Pierce showcase another example of an interconnected voltage bus for your next CubeSat, in which the bus is now regulated to a strict 5 V power supply. All activity (Power in and out) happens through the power bus, while switches are directly linked from the bus to the component for regulated power. An I2C chip can be added to the circuitry to monitor charging levels and switch subsystems on or off. Because of the added complexity, the I2C chip can communicate to the PI 0 over the newly implemented PC/104 ISA interface on the powerboard. The figure below demonstrates the detailed bus design with the major components connected, their power usage and how each component interacts with each other.

Newcomers Guide to CubeSats, Jorge Rodriguez and others, 2019 | pg. 40

## Appendix C: QUAD CHARTS

Quad Charts were an item teams were required to submit monthly to the NASA CubeSat Launch Initiative (CSLI), who were providing our free launch opportunity. We provide one such quad charts to show the format and general 'at a glance' utility of these reports.

| | Mission Description Cactus-1 (Unified Capitol U CubeSat-1) will demonstrate the use of Silica Aerogel for the use of capturing and profiling micro space debris and micrometeorites utilizing the TRAPSat subsystem as well as testing the performance of high bandwidth IP based communications (CiV) against conventional amateur radio access.
Major Milestones 07/16 PDR 07/16 PCaM prototype RockSat-X test 09/16 CDR 12/16 component testing begin 01/17 FSW testing (delayed to 4/17) 07/31 Final integration & test 09/17 Flight Unit Shake & Bake complete 10/17 FRR 12/17 Delivery | Size 3U++ | Mass 2.8 kg+/- 15% | RF Power 0.5, 0.9 W | Configuration Tabs
| Deliverables Status RF License: FCC License submitted, working on SpaceCap ODAR: Will submit update NOAA: approved (n/a) MSPSP: Submitted | | Issues/Concerns Waiting for frame to ship. Also trying to figure out how to attain a tab dispenser.

# CACTUS-1

## Capitol Technology University

<MONTH> 2016

Newcomers Guide to CubeSats, Jorge Rodriguez and others, 2019 | pg. 41

## Appendix D: CACTUS-1 Original Proposal

[This is the initial technical description of our Cactus-1 mission. Notice that, as our proposal evolved, we change the name of our mission from “CapUSat” to “Cactus-1” (Combined Advanced Capitol Technology University Satellite-1). T his writeup below is provided for inspection purposes to other teams and is not the final draft of our proposal-as-awarded. We also include R. Schrenk's technical description as a support document.]
Our “CapUSat” (Unified 'Capitol U' CubeSat) mission is the capstone following our lab and high altitude balloon development programs, where our tested student-initiated projects can be deployed in their target orbital environment to demonstrate crosscutting and innovative technologies (Objective 1.7) and proving our detector technology is suitable for future use in profiling the content of the interplanetary medium (Objective 1.5). Our payload has 2 primary technical goals:
* Operate the Particle Capture and Measurement (PCaM) aerogel payload in orbit with sufficient cadence to yield debris and particle measurements of the near-Earth environment, and

* Use our CubeSat-via-Internet (CVI) commanding system to reduce the ground commanding 'footprint' by using ordinary internet utilities via a satellite internet provider (Iridium and/or GlobalStar) to increase bandwidth and reduce the need for custom commanding software.

Our tertiary technological goal is the use of aerogel et insulation as an effective lightweight thermal shield for CubeSats.

Our current work has a Technology Readiness Level (TRL) of 4, “Subsystem validation in laboratory environment” and we are moving to TRL 5, “Subsystem component validation in relevant environment”, through our multiple high altitude balloon missions and upcoming summer ballistic flight. Preparing then flying in low Earth orbit will enable us to reach TRL 7, “System prototyping demonstrated in operational environment- space”, a stage that can only be reached by an actual orbital flight. We intend to support this development at Capitol Technology University through our existing program incorporating classroom work, senior projects, and both internally and Maryland Space Grant Consortium funded internships.

Newcomers Guide to CubeSats, Jorge Rodriguez and others, 2019 | pg. 42

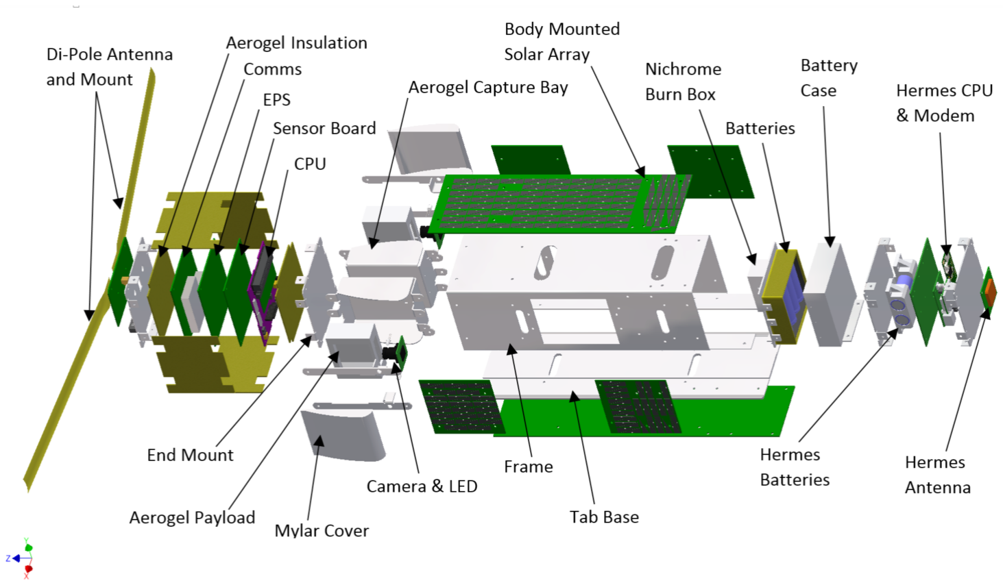
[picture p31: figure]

TECHNICAL DESCRIPTION
CACTUS-1
December 2016
Capitol Technology University Ryan M Schrenk
rmschrenk@captechu.edu

The overall goal of the CACTUS-1 mission is to profile and capture micrometeorites and micro-debris using aerogel in an effort to initiate the cleanup of LEO as well as provide a platform for a technology demonstration for an experimental communication and command subsystem, and verify our bus design (which itself is based strongly on open hardware designs).

The satellite will be launched as a secondary payload aboard Launcher 1, December 2017. It will be inserted into a Polar orbit at at nearly circular roughly 500 km semi major axis, on an

Newcomers Guide to CubeSats, Jorge Rodriguez and others, 2019 | pg. 43

inclination from the equator of or near 90 degrees. Cactus-I will deploy unpowered and be able to receive communications after a charging orbit. Transmission of health and safety telemetry and payload data occur when commanded by the ground and are capped by the flight system at no more than 10 minutes in duration (or when a turn-off is received, whichever comes first). The satellite is also capable of short periodic health-and-safety packet transmissions. The satellite will have a toggleable capacity to respond to amateur user ‘pings’ with a short return telemetry packet to encourage educational use.

Our minimum mission success criteria is two weeks of working operations; our nominal mission duration for scientific results is 3 months; our extended optional mission duration is 2 years. Atmospheric friction will slow the satellite and reduce the altitude of the orbit, along with negligible mass increase and energy from likely impacts, will help to slowly de-orbit the satellite. De-orbiting timescales will be assessed as per the ODAR (Orbital Debris Assessment Report). The spacecraft is a single 3U unit with the dimensions of approximately 36.6cm x 10.3cm x 11.0cm, based from our launch provider IDD (Dec 2016). We using the cannister tab design (rather than the older rails style). The total mass is roughly 2.75 kg.

SUBSYSTEM DESCRIPTIONS:

Guidance, Navigation and Control (GNC) Subsystem:
The CACTUS-1 spacecraft will be utilising Passive Magnetic Attitude Control or PMAC to accomplish GNC. PMAC is comprised of a pointing magnet and hysteresis rods for angular momentum dampening. Since this system is passive we have no true GNC subsystem and no orbit corrections can be made.

Command and Data Handling (C&DH) Subsystem:
The C&DH for CACTUS-1 utilizes a main frequency 433.050-434.790Mhz. This is accomplished through using a Radiometrix TR2M-433-5 multi-channel transceiver with AFS2-433 RF power amplifier. The Antenna is a full wave dipole tape antenna. The system is controlled by a PiSat board running NASA’s open source Core Flight Software (CFS).
The second or experimental Hermes comms system is comprised of an Iridium modem 9603 N transceiver and a helicoil 48mm antenna.

Newcomers Guide to CubeSats, Jorge Rodriguez and others, 2019 | pg. 44

Electrical Power Subsystem (EPS):
The primary EPS is a direct energy transfer system using the solar array to produce 3.08W average. This is composed of (6) 1U and (2) 0.5U solar panels using Trisol 28% efficient GaAs triple junction solar cells, it utilizes (4) COTS LG 18650 3.7V 28090 mAhr Lithium ION battery cells. The EPS drives the primary PiSat board, which acts as the distribution hub for the sensors and payloads. Nominal power usage is 1.77W with an additional +1.1W when transmitting.

The Hermes secondary payload experimental EPS consists of (4) 0.5U solar panels using Trisol GaAs 28% efficiency solar cells, and (2) COTS LG 18650 battery cells. Hermes will utilize the smart technology within a power bank to distribute power evenly throughout the system. Hermes will use a fractional duty cycle for use and spend the majority of its time powered off and charging, with short experimental use of the Iridium modem.
To turn on the entire CubeSat, there are two powered inhibit switches and 1 SW timer to ensure that the spacecraft is triggered on when launched from the launcher.

Thermal Control Subsystem (TCS):
The TCS insulates the card stack of the CubeSat with Aerogel eting insulation. The CubeSat will have embedded sensors within all systems to monitor thermal anomalies through the PiSat boards and transmit the temperature data. If any temperatures reach a certain threshold that is considered unsafe, there will be a set of RTS commands and procedures to maintain the temperature such as; deciding which sections to turn on or off, or speed up or slow down the processor or hibernate until temperatures reach a safe and nominal threshold.

Structure Subsystem:
This structure is a 3U++ canisterized payload (based on 12/2016 IDD). The structure is fabricated with 7075 Aluminum for the outside structure. (Details on the significant layouts and designs)

Propulsion Subsystem:
There is no propulsion subsystem integrated within the spacecraft.

Newcomers Guide to CubeSats, Jorge Rodriguez and others, 2019 | pg. 45

Pressure Vessels:
There are no pressure vessels. The possible hazardous or exotic material is that we are using silica aerogel as an orbital debris capture mechanism, as a two 51mm x 51mm x 13mm pieces. We are also using aerogel eting encased in kapton tape as insulation in our thermal et.

Payload Subsystems:
TRAPSat (TRapping with Aerogel Prototype Satellite) will be used to capture micro-meteorites and other various types of space debris. This system will include Silica Aerogel monolith as the main instrument for the capture and a camera to take a picture of the Aerogel. The Aerogel will be placed within a 3D printed RASC (Raised Aerogel Support Container) for secure placement. The data collection will be stored through the PiSat compute module. The second payload, Hermes, will use COTS Iridium 9603 Modem to serve as an experimental communications payload while utilizing the orbiting Iridium Constellation of satellites. This system will use a Raspberry Pi Zero as the compute module. By incorporating these payload in this 3U CubeSat mission, this will be one of the few CubeSats that has two integrated payloads on one mission. CubeSat material/construction description. The primary CubeSat structure is made of Aluminum 7075. It contains all standard commercial off the shelf (COTS) materials, electrical components, PCBs and solar cells.

Newcomers Guide to CubeSats, Jorge Rodriguez and others, 2019 | pg. 46

## Appendix E: Day in the Life test

Cactus-1
Day in the Life Report
July 9 2018
Alex Antunes, PI, aantunes@captechu.edu
A. Scope and Overview

The purpose of this document is to provide verification of the Cactus-1 day-in-the-life for ELaNa XX. This provides verification of the operations of the primary Cactus-1 bus and the TrapSat payload module. We performed the below set of operations prior to and after our vibe testing and thermal vacuum.

We note that the remove-before-flight pin and Day in the Life test of the Hermes Iridium modem payload cannot be performed due to licensing; once the Hermes system is active, it operates for 7 days then shuts down and deletes all software to ensure full compliance with the FCC shut-down and terms of the 7-day Iridium license. As the Hermes module is a stand-alone bolt-on secondary payload, it is not within the needs nor scope of thsi test.

B. Test Overview

This functional test covers two scenarios. The first is Initial Deployment and Power-up of the Satellite, testing the footswitch power inhibits, the boot-up procedure, and the autonomous release of the antenna via a burn wire circuit. We then include a 'standard orbit' test of the spacecraft being contacted and performing its data sequence and downlink, in order to test payload system functionality.

For these tests, for the initial burn wire to release the antenna, we substituted an LED for the burn wire to avoid having to open the satellite to replace the burn apparatus. The burn release

Newcomers Guide to CubeSats, Jorge Rodriguez and others, 2019 | pg. 47

test of the wire and the antenna were carried out earlier at a component level in a small vacuum tank, and also tested in a high altitude balloon flight.

The full sequence is below. Items in italic are test procdures that would not occur in actual flight, but that we do as monitoring during lab tests to provide additional analysis data.

1. The footswitches are depressed.
2. The remove-before-flight pin is removed from the main satellite.
3. The footswitches are released.
4. After waiting an estimated minute for boot-up, we use a network connection to verify the satellite has powered up.
5. The automatic antenna deployment command is seen (via #4) to occur at time + 15 minutes. (We keep the burn wire inhibit; no actual burn occurs during testing)
6. An initial camera data image pair is taken autonomously by the TrapSat payload.
7. After a wait of 5 minutes, representing a period of satellite operations, we initiated a data gather:
a. a 'transmit data' command is sent
b. automatically, all health-and-safety systems are polled
c. then, comms tranmission is initiated to transfer this health-and-safety packet
d. then, comms transmission ceases and the comms device is powered down to save power
e. automatically, a new pair of TrapSat camera images are taken (for downlinking at the next contact)
8. The satellite returns to its sleep/wait state until another 'transmit data' command is received.
C. Test Results and Conclusion

The most recent test was carried out on July 6, 2018 (immediately following oru therma-vacum tests). The sample health-and-safety packets from ground are shown below. The sample image

Newcomers Guide to CubeSats, Jorge Rodriguez and others, 2019 | pg. 48

files were generated and are attached; they are dark (as expected) because there was obviously not the sunlight illumination that we expect in orbit (the payload expects passive solar illumination to get clear images).

The initial boot sequence and data sequences both function. No transmissions occurred other than at the commanded times. The health and safety data is appropriate and matches ground tests. No anomalies were found.

Sample health-and-safety packet:

WJ2XBN Cactus-1:04-Jul-2018 01:34:54UT:GPU/CPUtemp=32.6C,32.552C:Temp=24.60C,Pre=99428.00Pa,Alt=158.30m:ADC =3344,3168,3120,4256:Mag=-360,-1721,-684.

Cam 0 test data:

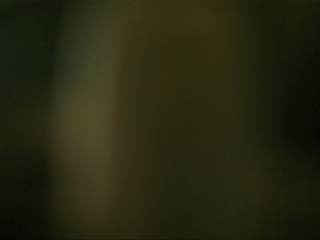
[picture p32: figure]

Newcomers Guide to CubeSats, Jorge Rodriguez and others, 2019 | pg. 49

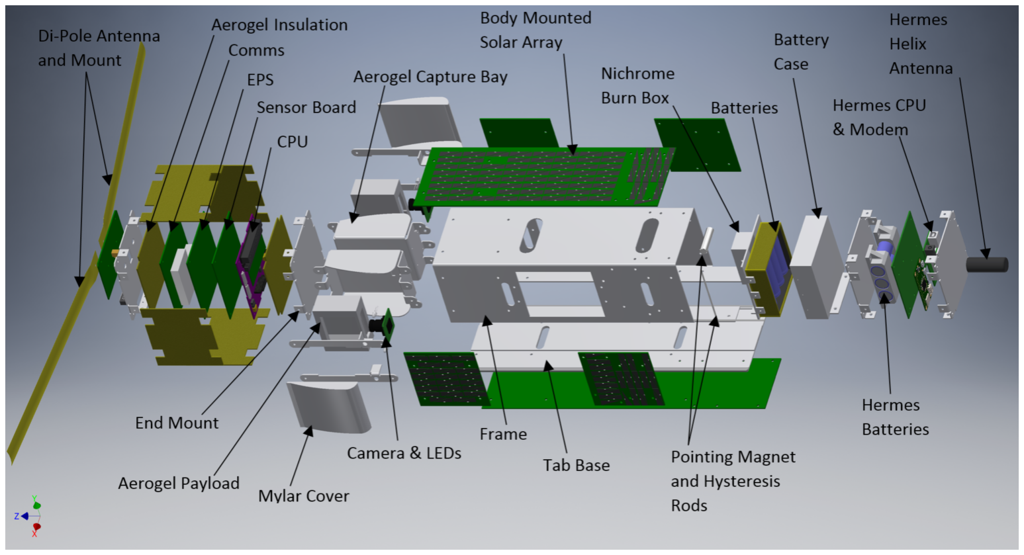
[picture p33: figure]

Figure 1: CACTUS - 1 Expanded View

Newcomers Guide to CubeSats, Jorge Rodriguez and others, 2019 | pg. 50

## Appendix F: Additional Resources

In addition to our Capitol CubeSat Cookbook Vol. 1: Engineering Guide, this document (Vol 2.: Newcomer's Guide), and Vol. 3: Designing a Common Electrical Powersystem), the links below are additional CubeSat references.

List of NASA Preferred Reliability Practices https://oce.jpl.nasa.gov/preferred_practices.html

Environmental Compliance Definition https://www.rmagreen.com/rma-blog/what-is-environmental-compliance

AeroSpace Failure Review Board Guidance Document http://aerospace.wpengine.netdna-cdn.com/wp-content/uploads/2015/04/TOR-20118591-19-Failure-Review-Board-Guidance-Document.pdf (http://aerospace.wpengine.netdna-cdn.com/wp-content/uploads/2015/04/TOR-20118591-19-Failure-Review-Board-Guidance-Document.pdf) Pg 18 & 22 for UVF

NASA CubeSat 101
https://www.nasa.gov/content/cubesat-launch-initiative-resources
CubeSat 101: Basic Concepts and Processes for First-Time CubeSat Developers (pdf) (https://www.nasa.gov/sites/default/files/atoms/files/nasa_csli_cubesat_101_508.pdf)

How to do research with a professor https://www.cs.jhu.edu/~jason/advice/how-to-work-with-a-professor.html

Student Team Projects: Tips to Complete a Successful Remote Project https://collegepuzzle.stanford.edu/student-team-projects-tips-to-complete-a-successful-remote-project/ (https://collegepuzzle.stanford.edu/student-team-projects-tips-to-complete-a-successful-remote-project/)

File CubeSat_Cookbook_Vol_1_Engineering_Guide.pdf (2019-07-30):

The CubeSat Design Handbook is a product by Robert Pierce Smith.

@ 2018 Robert Pierce Smith, all rights reserved

Acknowledgements: The Cactus-1 mission is Capitol Technology University's first CubeSat mission. Our launch opportunity was provided via the NASA CubeSat Launch Initiative. The Cactus-1 mission is supported by grants from the Maryland Space Grant Consortium (MDSGC).

# CACTUS-I Design Documentation and Future Guidance

Pierce Smith

12/19/18

Credit to Xtenti

Smith 2

## Contents

## Purpose

The purpose of this document is to capture the design of the CACTUS-I CubeSat. The design as well as the designs behind the design will be explained. A ‘Lessons Learned’ will be provided for each section to define what went well and what did not go well. This information is specifically called out in hopes that a future group of student engineers may learn from them and reach higher goals.

## Contents

This document will cover Solar, Power, Structure, and Systems design details. This document will not discuss the CACTUS-I ACS, Software, Communications, and ground system in detail, some topics will not be discussed at all. This document will not discuss the paperwork behind the mission; proposal, ODAR, FCC licensing, and MSPSP forms.

## Note

Some sections of this document will speak negatively of certain aspects of the project. To clarify, CACTUS-I is a large success because it made it to the launch pad despite the constraints on the students and PI. The point of discussing the failures and negative aspects of CACTUS-I is to improve upon the program and strive for a better CACTUS-II, not to place blame or point fingers. Many faults discussed are ones I see in hindsight and they are often my own mistakes.

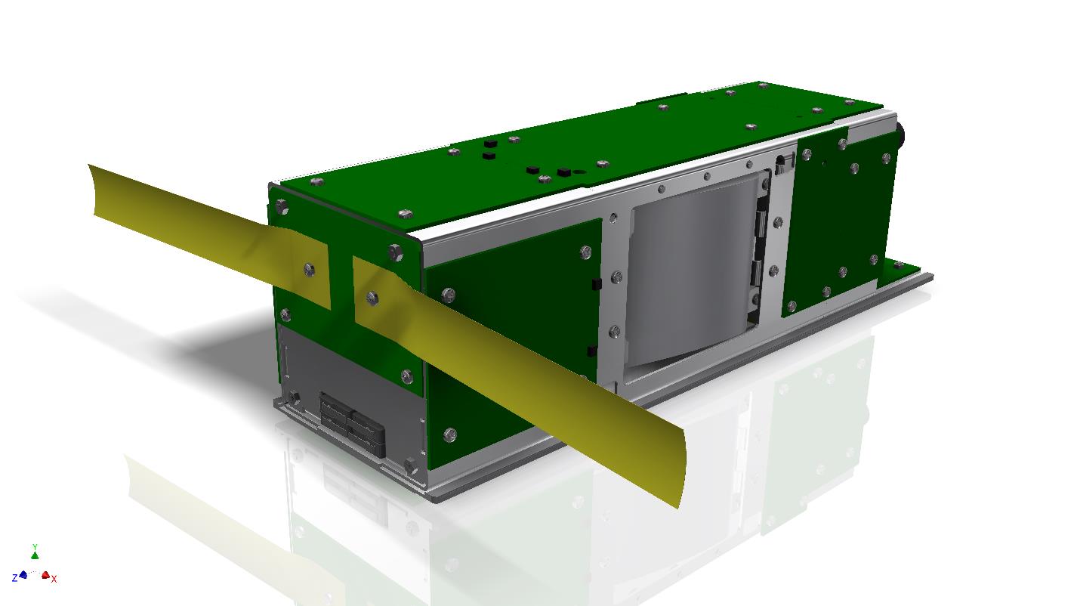
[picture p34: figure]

Figure 1- CADD Render of the CACTUS-I CubeSat | Credit to Pierce Smith

## CACTUS-I Overview

Capitol Technology University’s CACTUS-I is a 3U++ Tabbed CubeSat, meaning it is 366 x 116 x 113 mm satellite using the new Tabbed launching system (interface details in the structure Section). The goal of Capitol’s first CubeSat is to support two payloads that have been developed in the past 3 years; TRAPSat and HERMES. TRAPSat is a debris collection, imaging, and profiling subsystem with the goal to map out debris clouds in orbit. HERMES is an experimental communications payload using the Iridium constellation for uplink and downlink communications. The chosen orbit was a Polar orbit (Altitude undisclosed), driven mainly by TRAPSat’s desire to collide with debris which is more common at the poles. The satellite has a planned lifetime of 3 months with extended missions possible as far as the space craft survives.

The CACTUS-I budget was under twenty thousand dollars while the Satellite itself cost about Ten Thousand dollars. No Students or Faculty were paid during the development. All funds went towards materials, tools, and supporting infrastructure built/bought at Capitol. The project was built almost entirely by students. The team size varied from 20 during research, profiling, and brainstorming phase (phase A) to just 5 during the integration and test phase (phase D). The development time started August 2016 with delivery in early 2019. CACTUS-I passed all launch requirement and testing requirement and is approved for launch.

Figure 2, below, is an exploded CADD model of the CACTUS-I CubeSat. From right to left are components for the card stack, TRAPSat Payloads, Frame and solar panels, CACTUS-I batteries, and the HERMES Payload. The card stack consists of the Di-pole antenna and mount, the Aerogel insulation, Comms, EPS, Sensor, CPU, and End mounts. The TRAPSat Payload components are the Mylar Cover, Aerogel payload, Camera, LEDs and Aerogel Capture bay (ACB). The CACTUS-I batteries on the left side are pointed out as the battery case and batteries.

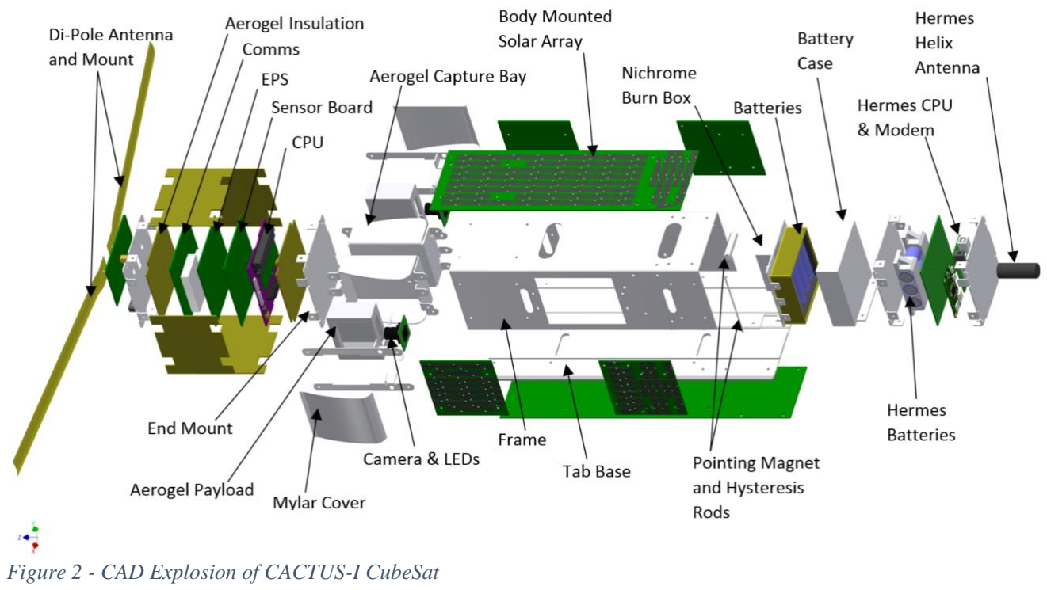
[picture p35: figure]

Figure 2 - CAD Explosion of CACTUS-I CubeSat

## CACTUS-I System Design

Constraints
The CACTUS-I mission had many risks and constraints affecting Schedule, Cost, and Scope. These are all due to Capitol being a small school with little resources that has never launched a CubeSat before. This risk was well known and understood before starting the project. Additional constraints were set on the project before it began; the CubeSat was to be built for under 10000 dollars and built in 1 year.

It terms of cost, the overall project budget was low. The additional constraint of the CubeSat itself costing under 10000 only added to the challenge. The typical trade study determining buy or build was not effective because almost all CubeSat subsystem solutions cost $5,000 dollars. Buying solutions that were not specialized for CubeSats were also looked at but finding subsystems that met most of the needs was difficult because of the niche CubeSat industry. Much of the budget was spent on supporting resources like soldering stations, test equipment, software defined radios and other radio equipment. To show proportions, two pie charts have been created. Figure 3 below represents the total spending on the CACTUS-I mission. Figure 4 further below shows the spending on just the CubeSat, the total estimated cost of the CubeSat is $9,300, meeting the goal of building a CubeSat in under $10,000.

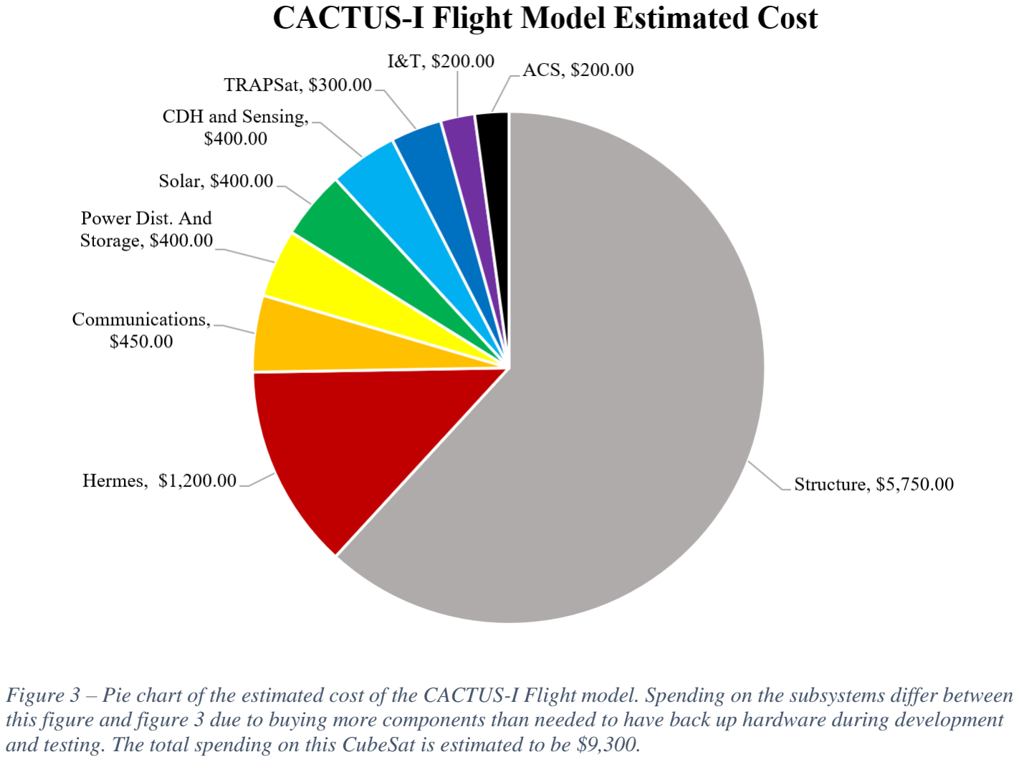
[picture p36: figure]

Figure 3 – Pie chart of the estimated cost of the CACTUS-I Flight model. Spending on the subsystems differ between this figure and figure 3 due to buying more components than needed to have back up hardware during development and testing. The total spending on this CubeSat is estimated to be $9,300.

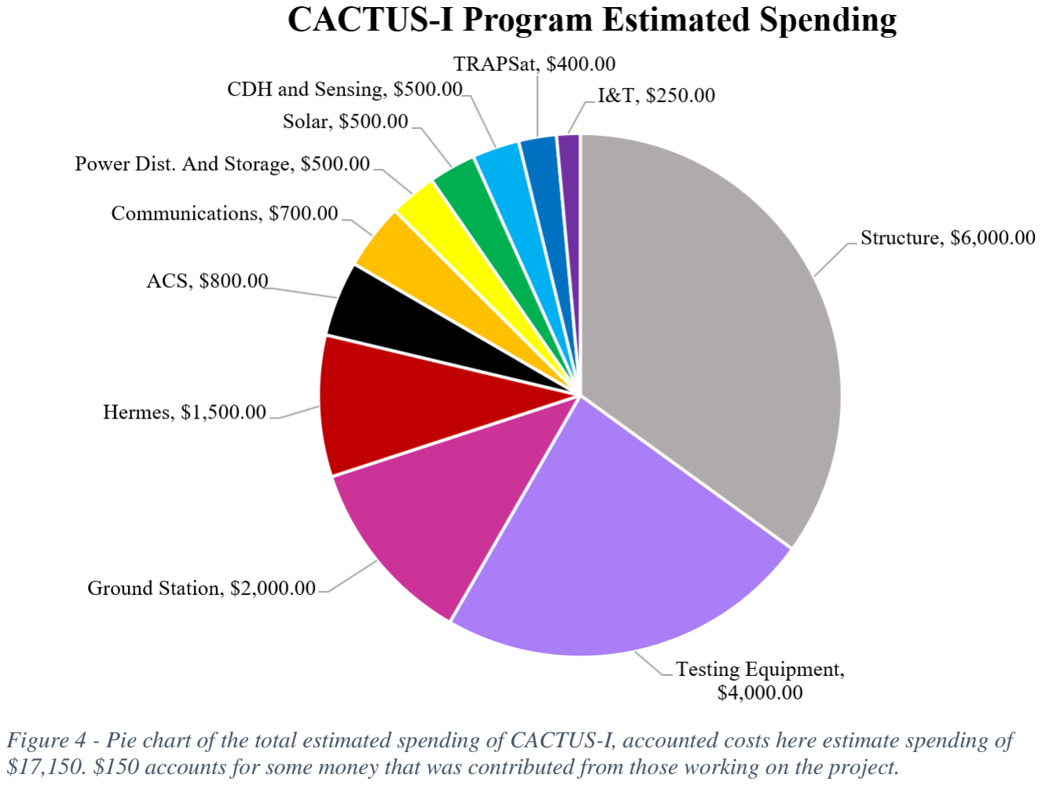
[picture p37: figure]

Time and Schedule
CACTUS-I Development started in August of 2016 and the delivery date at the time was set for August of 2017. This was an aggressive schedule driven by one of the goals: build a CubeSat in under a year. This goal was a large risk to the project because much of the time during that year would have been taken up by turnaround time from machine shops and PCB houses. Dates for mission delivery slipped and as they slipped, so did the project’s end date. This worked well with our development as CACTUS would have been nowhere near done by the original deadline. Many risks that came to fruition contributed to the increase in development time. These risks included a lack of knowledge, the need to be flexible during development, and a decrease in student participation.

The lack of knowledge stems from the fact that the CACTUS-I team was led by sophomores and worked on by sophomores, there were very few upper classmen in the group. Those that led the project had worked on other sounding rocket payloads, giving them some experience in the space field, project lifecycle, and design. These skills were helpful but did not meet what was needed for CACTUS-I. For many students in the team, this was their first large project where there was design work to be done. Many students were new to large extracurricular projects which led to students learning as they went and experienced students spending time to teach new students rather than continue development. A lack of knowledge caused many subsystem designs being underdeveloped or containing mistakes, leading to rework. Mistakes created the need to be flexible in terms of what gets worked next, to cope with rework. The Gantt chart above shows work on many subsystems being dropped in favor for others and being picked

Figure 4 - Pie chart of the total estimated spending of CACTUS-I, accounted costs here estimate spending of $17,150. $150 accounts for some money that was contributed from those working on the project.

up again later. This was also done because no subsystem was fully defined from the start of development. Work needed to be halted in one subsystems and started in another in order to define the interfaces between to the two to continue design on both fronts.

As time progressed, students either lost interest in the project, felt that their involvement was no longer needed, or they had to stop working because of school work. As student labor began to dwindle for certain subsystems, development stopped all together. This can be seen by design items being worked in series rather than parallel. Those that remained on the team worked one subsystem at a time before moving to the next.

Scope
The scope of the CACTUS-I mission was one of the biggest hinderances. The problem with the scope of CACTUS-I was the goals that it attempted to achieve; built in one year and for under $10,000. These two goals set the stage for the rest of the project: rushed. CACTUS-I is capitol’s first venture into the CubeSat space. Creating a functioning CubeSat is enough of a challenge for a first-time university, what added to the challenge was the very aggressive scope.

To keep with schedule, CACTUS-I needed to be quickly designed, fabricated, integrated, and tested to meet the launch date in one year. This goal was unachievable from the start but was only realized partway through the design process. The project got a much-needed break from the many schedule slips of the launch provider. This provided the project with needed time to complete the build. Without these schedule slips, CACTUS-I would not have been ready for launch.

The goal of completing the CACTUS-I build for under $10,000 was fitting given Capitol’s reputation of delivering performing systems on a very low budget. The reputation that is being referred to is Capitol’s students’ ability to build low cost sounding rocket payloads that still achieve high levels of success (even in the event of a rocket failure). But as stated before, CubeSats are a new project space for Capitol. By holding the build budget to $10,000 it limited the project’s ability to ‘Buy or Build’ solutions. The commercial CubeSat market is very niche, so finding solutions that are not expensive qualified flight hardware is challenging. Despite these challenges, the CACTUS-I CubeSat was built for just under $10,000, meeting its goal.

Design Choices
Attitude control system
The general requirements for the attitude control system were to keep the TRAPSat system pointed in the direction of the velocity vector and enable communications when desired. Other drivers included minimizing cost, complexity, and the SWaP properties of the subsystem. The type of subsystem chosen was a Passive Magnetic Attitude Control (PMAC) system. This type was chosen because it required no input power, it did not take up much space or mass, and it did not require any form of commanding or control. A PMAC system is operationally simple but very complex during development. Simulation (through MATLAB) is required to determine exactly how much hysteresis mass to put in each axis and how strong the dipole of the pointing magnet should be. These parameters required many simulations to determine the proper amount. This increase in complexity during development was accepted because simulations could be run overnight, and students could work on other tasks while ACS was being simulated.

This PMAC system was able to meet the needs of the TRAPSat science payload by keeping the CubeSat aligned with the magnetic field lines of the earth, the satellite would flip 180 degrees when going over the magnetic poles, but this was accepted because of the cheap and elegant solution that PMAC was to the mission. This imposed another constraint of the CubeSat from the science payload; the TRAPSat payload needed to be mounted on both sides of the CubeSat so that one payload is facing the velocity vector at all times.

Power systems
The CACTUS-I Power subsystem requirements were very open ended because not many portions of the satellite were defined. The solution must provide power for a Raspberry Pi and the communications subsystem. The subsystem must follow the PC104 standard, physical is required, electrical is preferred. The solution must be low in complexity as not many students are experienced in electrical engineering and design.

The need for a PC104 size leads down three avenues, buy, build from another university, or create in house. Buy is out of the question as buying space craft subsystems is too costly. Building from another university was considered, many designed were looked at from other universities but the issue was that there were almost no solutions that were fully documented, allowing Capitol to replicate the design. This led eventually to building in house. Originally the design for the power board came from the company inter orbital CubeSats free of charge. This design was chosen because the communications solution came from the same company, meaning that two subsystems were more likely to work, making integration easier. The board was simple for teammates to understand, it supplied exactly what was needed to the communications system, and it could be replicated at about the same price for an in-house creation. The board did not meet the required 5V supply for a Raspberry Pi so the design was modified once received from the company. During development it was realized that the inter orbital design suffered from the same problem as the university designs, not enough documentation. The power board was changed heavily over time, making different functions more efficient and reliable and meet the missions needs exactly.

The batteries used in the power system were a simple choice. 18650 cells were purchased from Panasonic (part number NCR18650B), as recommended to the team from an experienced professional. Power storage most definitely had to be a buy solution for the power subsystem.

Mechanical and Physical
The Mechanical subsystem had major constraints relating to the deployment system as well as the launch provider. These constraints were mainly vibrational, physical size, and surface characteristics. During development the structure subsystem was given priority as it would be the most expensive and have the longest turnaround time. During early concept design many CubeSat frames were found for sale. These frame costs were used as an estimation of cost for the custom structure to be built for CACTUS-I. It was understood that should the custom design exceed that cost estimation; a commercially available frame should be purchased. A design from Planetary Systems was used as inspiration; a single part was used to meet the mating requirements of the tabbed interface between the launcher and the CubeSat. Thus, vibrational and physical size requirements flowed to the rest of the CubeSat Structure parts. With this allocation, all parts needed to meet the physical size and vibrational requirements but only one part needed to meet the tabbed interface requirements as well. This reduced cost as only one part needed extremely high specifications while others could lack tolerances that were not needed.

The design of the mechanical system was also the design of the physical layout and location of all components. The TRAPSat payload required to be facing the velocity vector

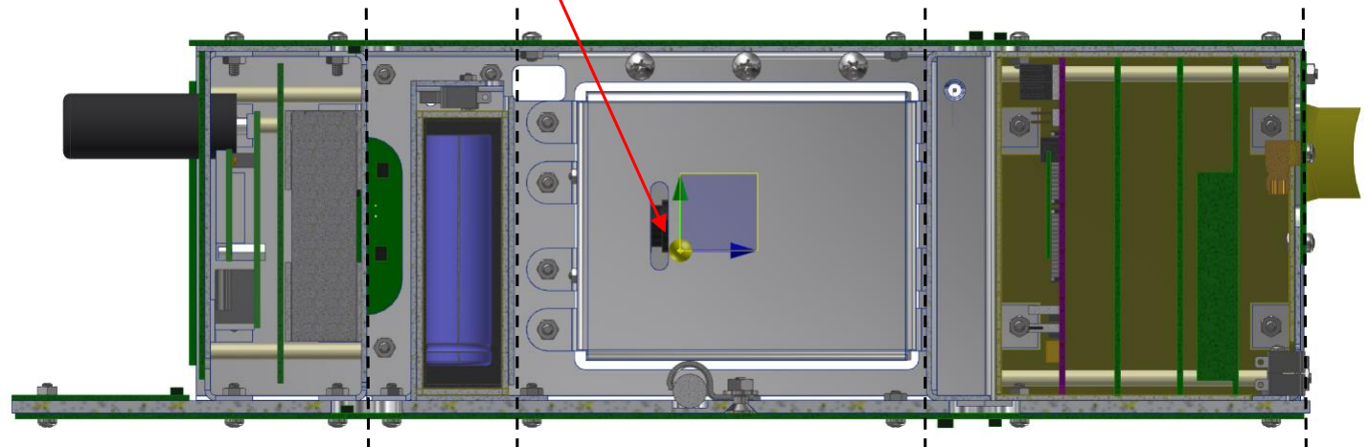
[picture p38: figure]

during orbit. The mechanical design was laid out such that the axis of the PMAC pointing magnet aligned with the TRAPSat Payload’s. This meant that there was a TRAPSat payload on the front and the back of the CubeSat. With the HERMES on one end of the CubeSat the TRAPSat payloads were placed in the middle. The TRAPSat payloads are very light so placing them on the opposite end the HERMES Payload would shift the center of gravity towards the HERMES end. Placement was an effort to balance center of gravity for the space craft. The End opposite to the HERMES payload is where the PCB card stack was placed. As a final effort to balance the center of gravity the batteries for the PCB Card stack were placed next to the HERMES Payload.

HERMES Payload | TRAPSat Payload | Bus, PCB
Batteries

Center of

Figure 5 – Half Section view of CACTUS-I, revealing the distinct regions of the CubeSat

Lessons Learned
What Went Well
Successful ‘Final Push Efforts’ by hard working students to complete milestones.

Last push efforts occurred when the team needed to complete a task by a certain time to meet an internally prescribed deadline or milestone. The team members that stayed on CACTUS-I were hardworking and would meet the challenge to come to the lab to work for the whole day and night with the rest of the team. These times were often the most productive and most fun, keeping teammates coming back. Final Push Efforts occurred often as this type of progress is common with University programs because students still have to attend class and complete homework. Students focusing their effort on one day synchronously is extremely beneficial. Each Final Push Effort had great results. Internal deadlines were often not broken.

It is critical to find the right type of students for a project. The types desired, and the ones that stuck around, were the students that showed up reliably and worked. Sometimes these students had very little experience and other times they had a lot. The experience didn’t matter in the grand scheme. What was important was that the students showed up every time, stayed in the loop, and became knowledgeable on the CubeSat. These hardworking students are what make last push efforts and projects like CACTUS-I possible and successful.

Adaptation of designs and future proofing work helped keep the program rolling and keep schedule slip to a minimum.

Future proofing work is giving a design the flexibility to change configuration and adapt to problems, troubleshooting, or new designs. Consider two configurations, each has its tradeoffs and there has not been a conclusion as to which is better. To keep the program moving forward the design would be done in such a way that both configurations can be supported. In the case of structure and mechanical it’s imperative to get the design correct the first time so that nothing physical needs to be reworked. Physical rework costs time and money. This is less apparent on the software side as it only costs time. Student labor (or PI labor) is cheap. Future proofing structure and PCB designs was critical to keeping those subsystems on track.

In typical engineering, a waterfall style of approach, it’s more important to know exactly how everything will fit, form, and function together. A CubeSat will often have unexplored territory within its own design space, leading to discovery of work. This unknown can cause long holding patterns in a typical engineering process. Future proofing designs allows for the program to continue into those unknown spaces with a design that can adapt and support many configurations. This modular, adaptive approach is seen more in software development under the Agile design process although, it can be applied to more technical areas. CACTUS-I development fits a very loose Agile workflow. This workflow was necessary for keeping the program moving.

What Did Not go Well
Design choices involving heritage were not properly analyzed.

In class, students are taught that heritage is an important component of a space craft design, without heritage a design has no merit and no verification of performance besides ground testing. This of course is a bad thing, except in the CubeSat world. CubeSats are meant to be experimental, thus not many CubeSats will have heritage. Throughout development many decisions were derailed or put on hold as a lengthy discussion or civil argument over heritage took place. These discussions sometimes resulted in a good outcome and other times did nothing but slow down key decision making. Heritage can help a mission reduce the amount of work to be done to finish the build, but it can also hinder the project as well if there are better methods, product’s ect. available. The key problem was that not enough analysis was done to make some of these key decisions. A heritage design would often win over another design simply because it already existed and worked once. Documentation of a past design was typically minimal and therefore cost the program time.

When heritage was involved in design choices, decisions were made fast because team members were led to believe that a heritage design was the best choice. This mentality led to a lengthier I&T process because old or bad documentation led design astray or did not provide the needed details. In the CubeSat space, it is important that a team challenges a heritage idea the same way it would challenge any other idea. In reflection, very little of the design was looked over from a heritage perspective. There were very little questions asked about ‘What’s inside?’ Although, these questions may not have been asked due to program issues not on the CACTUS-I side. For CubeSats, a good idea, a decent design, decent testing, and documentation to back it up will be more than enough to fly.

## CACTUS-I Structure Design

Major Design Features
The CACTUS-I structure has 4 primary components; The Tabbed Sled, the Bus Shell, the TRAPSat Shell, and the HERMES Shell. The Tabbed Sled received its name because it stretches the entire length of the CubeSat, serves as the mounting platform for all CubeSat components and is the interface to the launcher. Each shell represents 3 sides of a cube where the fourth face has small flanges that allow it to slide on the Sled, see figure 6 for a shell model. The Tabbed Sled has channels that are 0.06 inches deep, allowing the flanges of the bent metal shells to sit flush with the top surface. The shells are fastened to the sled with no less than 4 screws.

The shells allow for modularization as
each segment of the CubeSat can be

constructed independently and integrated electrically on the bench, then mounted together physically. A shell only covers three faces of a cube with the fourth face containing flanges. This fourth face is properly covered when mated to the Tabbed Sled. The top and bottom (or front and back) of the shell will not be covered. This is left open in the case of the TRAPSat Shell to mount large components inside. The HERMES and BUS Shells are closed off by End Mounts, which allow for PCBs to be mounted safely. The shell is also used to mount solar panels, which cover most faces on the spacecraft.

Space is very tight within the CubeSat so one screw may be used to hold together many components. For example; A screw used in the BUS Segment is inserted from the outside of the space craft through a solar panel, through the Tabbed Sled, through the BUS Shell, and through a metal end mount where a press nut is attached, thus fastening all components to each other. This type of fastening is how solar panels and shells are fastened to the Tabbed sled. This is also how a solar panel, Shell, and End Mount are fastened together. This leads to less wasted space due to fasteners but increased integration complexity and time as three components are being fastened at a time.

Figure 6 – the Tabbed sled CADD model from the CACTUS-I project. The two channels on either side of the mounting plate is how the main components, the Shells, are aligned and

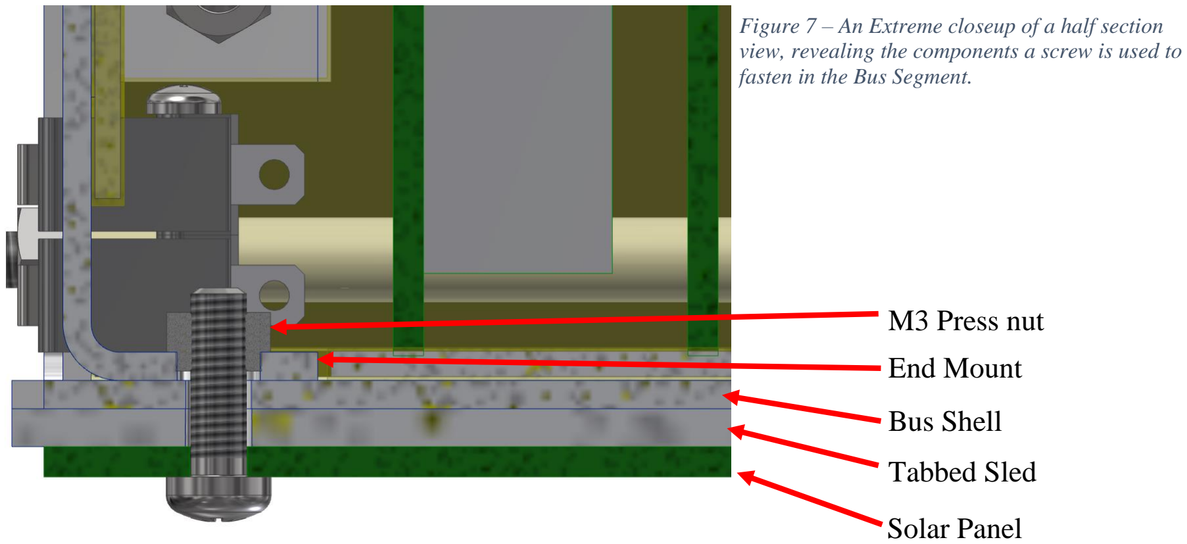
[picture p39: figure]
Solar Panel; Tabbed Sled; Bus Shell; End Mount; M3 Press nut; fasten in the Bus Segment.

Overview of Interfaces with Launch Provider
All references to X, Y, Z dimensions are based off the FANTM-RAiL™-Tabbed 3U Single (FRA-T3S) Attachment/Deployment Assembly Interface Description Document (IDD) provided to the team from Xtenti. The Tabbed deployment method is a new form of CubeSat deployment. CACTUS-I will be using the FANTAM-RAiL-Tabbed 3U Single (FRA-T3S) system developed by Xtenti. This system will hold the CubeSat by two hard anodized tabs and deploy by pushing with a constant force from a pusher bar located on the -Z Face.

The CACTUS-I Tab interface has extremely tight and specific tolerances as well as a hard-anodized surface. The nominal values of dimensions were used in CAD designs, these interface constraints were defined first before other design choices were made. The CubeSat was constrained to a maximum length of 113mm in the X direction and 116mm in the Y direction. To keep the design similar to CubeSat designs already existing, the CACTUS-I structure was chosen to be 100mm x 100mm in the X and Y directions, leaving space (6.5mm per face at least) for solar panels to be mounted to the surface. Performance parameters of other CubeSats can be related to CACTUS -1 with ease as less has changed between designs.

Many design choices were guided by Planetary Systems documentation because within the IDD, Xtenti directly references the Planetary Systems CubeSat specification as being the target satellite for deployment:

“… designed for up to a tabbed 6.0 kg (13.2 lbm) 3U UCP generally adhering to
the Planetary Systems Corporation (PSC) Canisterized Satellite Deployer (CSD) specification.”

Following the CSD specification from Planetary Systems was the best course of action in order to keep interfacing issues to a minimum with the Xtenti FRA-T3S deployment system.

Figure 7 – An Extreme closeup of a half section view, revealing the components a screw is used to

Material Choices
The Tabbed interface was chosen to be made of one machined plate of Aluminum 7075, 3mm thick, as recommended by Planetary Systems (Give Ref). The 3mm thickness was chosen to match the nominal dimension for the tabbed interface. The material was chosen because: 1) The majority of the FRA-T3S deployment system is made of Aluminum 7075, matching materials is desired for the same physical characteristics and
behaviors (thermal expansion for example). 2) The harder
Aluminum 7075 will hold up better than the standard
Aluminum 6061 against any wear and tear from handling, fit checks, and testing. Reducing the chance for the Interface to fall out of tolerance over time.

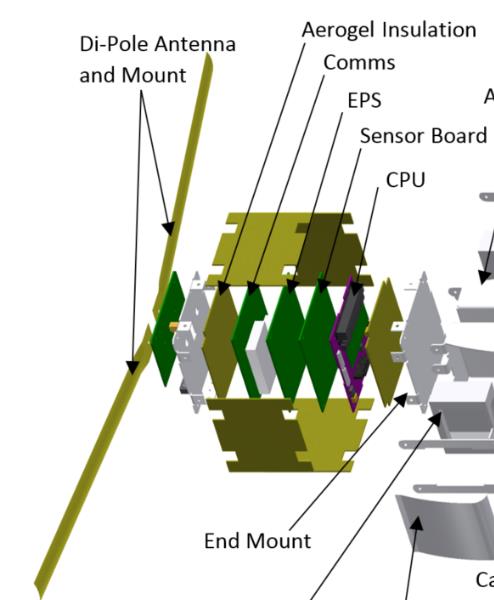
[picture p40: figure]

The rest of the frame was constructed with bent metal of thickness .06” and material Aluminum 5052. The thickness was primarily based off the Pumpkin CubeSat bent metal 1U frame as well as other CubeSat frames. The material choice of Aluminum 5052 was recommended to the team by a professional experienced in manufacturing. 5052 is more pliable and easier to bend than the harder 6061 and 7075. This leads to less cracks from bends and more dimensional accuracy post bend. Bending will create stress within the metal, over time this stress can be released, moving drilled holes out of place. It was explained to the
team that hole features on 7075 can ‘walk’ over time and
drift in dimensional accuracy.

The material of fasteners were typically Passivated 18-8 Stainless Steel because keeping as many components nonmagnetic increased the accuracy of magnetic attitude control simulations by reducing the real world ‘noise’ that could be created. PCB spacers are another primary component, separating PCBs from one another and giving clearance. The Material of the spacers flown is Nylon 6/6. Material was not a main driver for spacers, Nylon was chosen because of how custom the solution needed to be. Spacers that were 52 mm long were purchased and cut to the proper length. This saved money as spacers can be very expensive and it provided the custom lengths needed to meet the needs of the Card Stack design.

BUS Segment
The BUS segment is comprised of the BUS shell, the Card Stack, the Antenna PCB, and the corresponding solar panels. This segment is located on the end of the CubeSat, the -Z side. The Card stack is a stack of PCBs with End Mounts on the top and bottom, the antenna PCB is mounted on the outside of the top End Mount as it holds the Tape Measure Antennas. The bottom end mount is unique because it has a small chamber where the Nichrome burn will occur to deploy antennas. The Antenna end mount faces the exterior of the Space craft while the Burn end mount faces the interior, towards TRAPSat. This chamber is sealed off from the inside of the

Figure 2, with a focus on the left-hand side cord stack with Kapton tape and Mylar blanketing. The PCBs and End Mounts are separated and organized by long threaded rods running through the corners of the PCBs and spacers. Spacers give each PCB enough room top and bottom for soldered component clearance and wiring clearance. This stack is rotated sideways and inserted into the shell. With the End mounts and shell the card stack is covered on all faces except the bottom, which is where the segment is mounted to the Tabbed Sled.

TRAPSat Segment
TRAPSat is comprised of a the TRAPSat Shell, two Aerogel Capture Bays (ACB), the battery box, and corresponding solar panels. The TRAPSat segment is an open design where there are no end mounts on either side and there are modest openings in the Shell where the ACBs are mounted. The ACBs are mounted on either side of the TRAPSat Shell by 4 screws each. The Battery Box is only mounted to the flange portion of the TRAPSat shell via 4 screws as well. Because the box is only mounted on the flange of the shell, it is not truly fastened until the shell is also mounted to the Tabbed Sled.

HERMES Segment

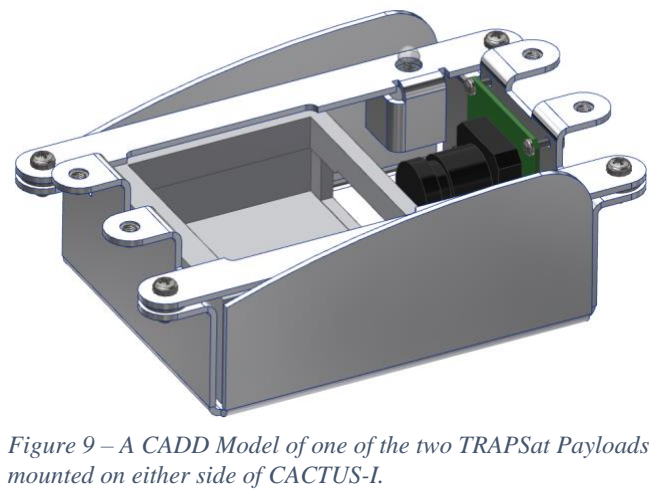
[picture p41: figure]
mounted on either side of CACTUS-I.

The HERMES segment is comprised of the HERMES card stack, HERMES Batteries, the HERMES Shell, and the corresponding solar panels. This design is very similar to the BUS Segment but shortened considerably to mount a static helix antenna. More detail on this design can be found in CADD models and other documentation from the HERMES Team.

Thermal
Thermal characteristics where not heavily considered because at the orbit CACTUS-I will be at, the temperature will stabilize between -10C and 10C. Mylar blanketing and Hybrid Aerogel insulation are the primary insulative materials used on CACTUS-I. Mylar Blanketing was used to cover the outside of the space craft to provide thermal insulation and good reflective properties. This blanketing was used underneath the solar panels as well because it is nonconductive, helping combat potential short circuits between a solar panel and shell, and because it could reflect heat shunted from the panels into the CubeSat. Hybrid Aerogel insulation packets were used to insulate the BUS segment of CACTUS-I on all faces. TRAPSat segment does not use insulation except for the battery box mounted within. The Battery Box uses the same insulation on all faces, protecting the sensitive batteries from temperature swings.

Figure 9 – A CADD Model of one of the two TRAPSat Payloads

Both thermal materials were mounted with double sided Kapton tape. This tape was used sparingly because the adhesive had a high outgassing percentage, making it dirty and difficult to use in a clean vacuum chamber. Using too much of this material would have hindered the ability to test CACTUS-I in a vacuum chamber.

Vacuum
CACTUS-I holds no pressurized containers, therefore each closed volume within CACTUS-I must vent within a certain amount of time. Each segment with a closed volume has enough open surface area to meet the venting requirements. The BUS section has open areas facing the TRAPSat segment. This was done because the TRAPSat segment has more than enough open surface area to vent itself and other closed spaces. The HERMES Segment has a thin but wide opening along the bottom of its exterior end mount, venting air directly into space.

Lessons Learned
Lack of tolerance between end mounts and Bus Shell affected the procedure for assembly but did not have any lasting negative effects

The clearance needed between the end mounts for the card stack and the Bus Shell were not considered in design. During integration, the card stack assembly could not be inserted into and through the Bus Shell because the End mounts were slightly too large. The end mounts could be inserted to be flush with the edge of the shell (as designed) and not farther. The original procedure had the full card stack assembly inserted. The modified procedure used to complete integration was to take off one on the end mounts, insert the card stack into the shell such that the end mount was flush with the shell, then the other end mount was put back on. During testing and fit checks, the assembly had to be taken apart. Clearance between the end mount and the shell became more reasonable but still required a modified assembly procedure. Tolerance between the end mounts and the shell should be considered. The end mount sizes should be reduced to allow clearance for the card stack to be inserted.

Screw heads and Nuts that protruded from the antenna PCB on the -Z face needed to be shaved or sanded to meet the physical requirements.

The outside of the card stack is where the antenna board is mounted. Screw heads and nuts protruded from the surface of the PCB. The Card stack and bus shell were recessed from the edge of the tabbed sled to ensure the protruding component did not violate the physical specifications of the CubeSat. The shell was not recessed enough because after build, the screw heads and buts protruded into the keep out zone on the -Z face. A Dremel was used to sand down the items and bring the CubeSat back into spec.

To keep this from happening, a low-profile nut and screw should be used on the outside of the card stack. The recessed card stack may also need to be re-evaluated to determine if it needs to be recessed further. A method of fastening the card stack together may also provide a more elegant solution to the problem of protruding components.

## CACTUS-I Solar Design

The CACUTS-1 Solar panel solution consists of PCB’s of varying size and small solar panel chips strung together to form a large panel. The output of these panels for the BUS and TRAPSat segment ranged from 10 to 13 volts. The size determined the amperage output, the smaller panels produced 40 mA at peak while the largest produced 200 mA at peak. The HERMES Segment uses a different voltage level, the output of these panels ranges from 8 to 11 volts. The amperage output of these panels ranges from 40 mA at the smallest and 100mA at the largest.

Materials
The chosen solar panels are small chip cells provided from TrisolX. These small cells were recommended because of high efficiency and dollar cost per area. These chips are the byproduct of cutting a large square panel out of a circular silicon wafer. See figure 10, right, for size.

CACTUS-I used leaded solder paste and solder (37 percent lead) to mitigate the risk of Tin Whiskers. Whiskering is not a well understood phenomenon that can be observed in most elemental metals and some alloys. Whiskering is more common with aged hardware and Tin Whiskers specifically are more common on hardware below 13 degrees Celsius. Figure 11 shows the potential of Tin Whiskers; the whisker pointed out is 18mm long and electrically connects one area to another. The mitigation of using leaded solder will drastically reduce the chances of whiskering to occur and whiskers to grow long enough to connect to another contact on a PCB. Figure 12 shows the difference leaded solder can make. The component has two leads that are tin plated, the lower portion of the lead was dipped in a leaded solder.

Figure 10 - TrisolX Solar Wing Chip product used to create solar panels. A total of 260 chips were

Figure 11 - This image shows long Tin whiskers that have grown long enough to contact another surface, 18mm long. This example shows that Tin whiskers have the potential to erroneously connect circuitry.

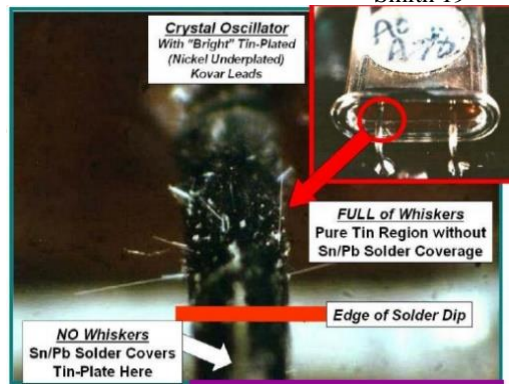
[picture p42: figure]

Another mitigation used was conformal coating of solder joints. Dow Corning 732 RTV Silicon Sealant: Clear was used for the conformal coating. A coat of less than 1mm was used on exposed solder joints.

Each solar panel also had a set of low drop diodes on each panel. These diodes prevented any forms of feedback into shaded panels. The power board that CACTUS-I used also had diodes for each panel input so the diodes on each solar panel ended up being a redundancy. A low drop diode is preferred to keep voltage losses to a minimum.

Direction on Manufacturing
PCBs were created in Eagle, a PCB creation tool owned by the Autodesk Company. This tool was chosen because it is free, easy to understand, and members of the team were familiar with this tool. The physical PCB was manufactured by a professional company.

To the right is an image of the Eagle layout of one of the solar panels. A gray-Red color represents exposed solder pad, this exposed pad shape almost matches the contact surface of the solar chips used. There is one corner of the solder pad that is removed, this was done to reduce the number of erroneous contacts from the bottom solder pad to the top contact of the solar panel. The chip itself is very thin and in
testing it was very easy for exposed solder to
connect to the top contact. The goal was to

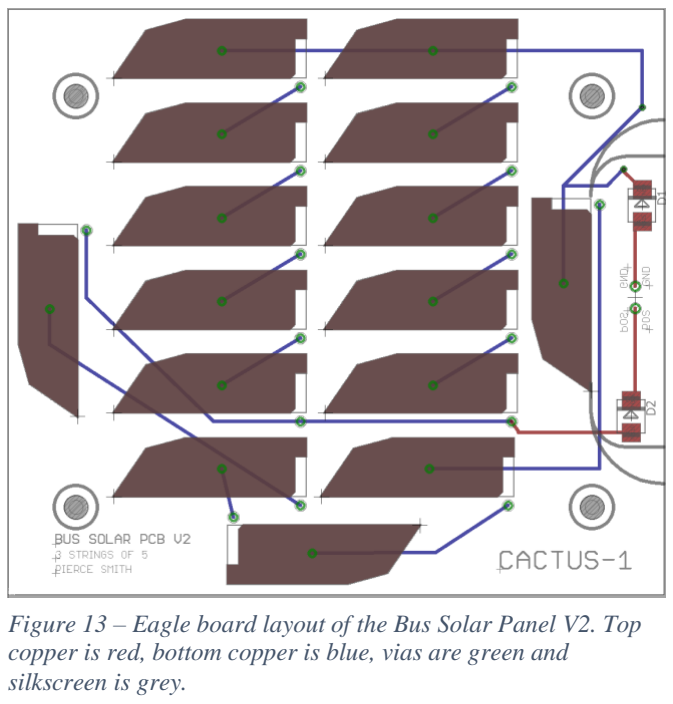
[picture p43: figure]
silkscreen is grey.

reduce the number of erroneous connections as fixing them took time and there was a high number of solar chips that needed to be soldered. Board traces are kept at a 16 mil width because of the relatively low power the solar chips will provide. Because trace space on the PCB is not a rare commodity thicker traces could have been used and is recommended.

The Process for creating a solar panel will be explained below.

Figure 12 - The crystal oscillator component above has leads that are Tin plated. These leads were dipped in a Sn/Pb based solder. Over time the Tin-plated section of the lead developed whiskers while the Sn/Pb dipped section did not. This shows the importance of using Sn/Pb based solder to prevent shorts and chances of failure.

Figure 13 – Eagle board layout of the Bus Solar Panel V2. Top copper is red, bottom copper is blue, vias are green and

1. With the boards in hand they were cleaned with isopropyl alcohol, front and back. The pads especially were cleaned as they were dirty due to the manufacturing processes.
2. Solder paste was applied to each solder pad. About a centimeter or more of solder paste was applied to the pad. Excess solder will be removed later.
3. A heat gun, on high, was lightly waved over the solder paste to liquify most of it. Heating continued until the paste fell from mostly solid to mostly liquid. This took about 5 seconds for the paste and heat gun used.
4. Solar chips were dropped onto each pad. Dropping from a centimeter off the PCB was the best strategy found as our fingers would not touch the solder paste and dirty the top of the solar chip.
5. The reflow oven was preheated and prepared with the heating profile used for the 37 percent leaded solder paste being used. If repeating this, use the manual that came with your reflow oven to see what heating profile should be used with your solder paste.
6. The PCB was placed inside the reflow oven when ready and the oven was started.
7. After reflowing has been completed the board was given time to cool off. Then the board was flipped over to wick away solder bubbles on any Vias. Isopropyl alcohol was used to remove the flux around each chip on the front and remove flux from each via on the back. Solder paste contains flux and as the paste is baked the flux flows out and away. This step should be performed within 8 hours after reflowing to reduce the chance of flux staining the PCB color (looks are super important of course).
8. Each chip was then heated with a heat gun to be flowed into the correct position. This is where the downfall of the PCB design is realized. The corner of the solder pad removed affected the surface tension of the solder, making the panel flow into a different spot on the pad. Each panel needed to be readjusted. This readjustment was done as part of removing excess solder. Extra solder would sit under the solar chip and raise it off the surface of the PCB. By using tweezers and gently pressing down the panel excess solder is pushed out. A wick can be used to remove the excess solder on the side. This process was easily accomplished with 2 people. One heating the chip and another adjusting the chip’s position.
9. The board was cleaned again, especially the tops of the solar chips
10. Wire jumpers were bent into an L shape to be soldered to the top contact of the Solar chip and the via placed next to the solar chip. The top contact was soldered first. The small portion of the L was placed on the solar chip top contact with the long leg placed in the via. The soldering iron was used to heat the wire while solder was fed onto the top contact pad. Solder tends not to grab the top contact pad right away, so practice is recommended to understand how to apply solder to this contact. This contact is a very thin layer of metal which can ablate off the solar chip if heat is held too long. When the top pad is removed, solder will no longer hold to the pad and the pad color will look silvery black. The chip will need to be replaced if this happens. The board was flipped over and the wire was soldered to the via. Heat was not applied for long to prevent heat creeping to the top contact and de-soldering. This process was repeated for each of the solar chips on the board.
11. The panels were cleaned again with isopropyl to remove solder material from the surface of the solar chips.

12. Low drop diodes were installed on either the front or back of the PCB, depending on the design. Flux and other material were cleaned off the diodes

Efficiencies
Each Solar chip had to be separated from each other to prevent short circuits, this leads to wasted space around each Chip. While these solar chips have a relatively high efficiency of 28 percent, the low packing efficiency of the PCB most likely offset this. The table below details the expected performance and efficiencies of each panel design. The Packing efficiency of the CACTUS-I solar panels is quite low, averaging around 32 percent. The total wattage potential of CACTUS-I is not calculated because it would be impossible to realize in operation. The efficiency of the cells used in calculations is 28 percent and the wattage per area used is 1390W/m²
. From these numbers is can be estimated that with full sun on one side, CACTUS-I can experience a solar power of 1.2 W (Bus panel plus the Pin/Blank Side panel) or 2.7 W (Bus panel plus Large Panel). The large difference in performance is due to the total area valuable for solar cells. The TRAPSAT payload took about 110 cm2 of usable surface area on two sides. With the proper orientation of the satellite, most direct sun will hit the higher performing sides of the CubeSat.
PCB Name | Bus (x4) | Large (x2) | Pin Side (x1) | Blank Side (x1) | Total
PCB Count | 4 | 2 | 1 | 1 | 8
PCB Total Area per Panel (cm^2) | 72.45 | 148.94 | 36.00 | 36.00 | 659.69
Solar Chip Count per Panel | 15 | 40 | 10 | 10 | 160
Total Active Chip Area per Panel (cm^2) | 19.50 | 52.00 | 13.00 | 13.00 | 208.00
Packing Efficiency (%) | 26.92 | 34.91 | 36.11 | 36.11 | 0.32
Predicted Power Output per Panel (W) | 0.76 | 2.02 | 0.51 | 0.51

Lessons Learned
Pad geometry led to manually rework of each cell, costing a lot of development time.

During the construction of the solar panels, the
largest drawback to the design of the PCBs was the
geometry of the Pad. As mentioned before, the corner of
the pad was covered by solder mask in hopes to reduce the chances of a short circuit between the jumper wire and the pad, see figure 14. This design choice ended up being a large time sink because after placing solar chips and reflowing them in an oven, the chips would be offset from
the desired positions due to the surface tension of the
solder. Because the corner of the pad was removed there

was lack of surface tension in that location, causing each solar chip to shift away from the corner. The Pad of the solar chip used in the PCB designs should be edited to include the corner

Figure 14 – PCB design view of a solar chip pad. Notice the bottom right corner of the pad does not have solder, dark red. Because solder could not grab at the corner of the pad, the solar cell would come to rest at a as copper once again. By doing so, solar chips reflowed will come out sitting in the right spots, ready for the next step of assembly.

The solar chip product used to create the solar panels led to a long and tedious build process.

There are a total of 260 solar chips used on the CACTUS-I mission. Each chip required manual rework and jumper soldering to function properly. A lot of development time went toward constructing these solar panels. These chips are expensive, small, and efficient. The small size meant that many would be needed to create one full solar panel. The small size also meant that the area available for solar panels had a lot of wasted space between cells. The high efficiently of the cells was nullified by the amount of wasted space between cells. The design of the solar panels should be reworked to use a different solar panel product. One that is physically large and consequentially more expensive. Seeking solar panels with a lower efficiency would be an excellent way to reduce costs. The outcome of this modification would most likely be a small increase in the yield of each solar panel due to better packing area efficiency despite a lower conversion efficiency. This would also reduce the amount of work and time needed to build the solar panels, allowing effort to be focused in other areas.

## CACTUS-I Power Design

CACTUS one power board was a solution reworked many times. This subsystem was heavily affected by the lack of knowledge and support. The power design originated from the inter orbital CubeSat kit. This board was chosen as a baseline because it came from the same system as the communications board, theoretically making integration easier. This was chosen because after many weeks of research, this seemed to be the easiest design to understand, build, and improve upon. The design had three main sections
to it: Power input and cleaning, charging, and power
distribution. Of the pieces reworked, the charging

section was modified to fit the battery design of cactus 1 and the power distribution section was also changed. The power input and cleaning stayed the same, although, 2 inputs were added to the chain to match the number of solar panels on CACTUS-I.

Design Overview
The power design is very simple. It relies on three sections that are each interconnected. The bus voltage of this design is driven by the current battery voltage. This means that all inputs and outputs must be regulated to account for the lack of control in the central power distribution.

Figure 15 – simplified view of the electrical system design.

The graphic above is a greatly simplified form of this design. Input voltage can go to either the battery for charging or it can flow directly to power distribution. This is a partially regulated system where bus voltage changes over time and all inputs/outputs must be regulated. Originally the design used li-ion batteries in parallel leading to a bus voltage of 3V to 4.2V. This lower voltage will create higher average amperages to meet the same power requirements. A higher amperage can increase the failure rate of small components. To keep the design reliable and cheap, the bus voltage was increased by changing the battery configuration.

Below is a schematic for the power board with sections previously mentioned marked with bounding boxes. Blue represents the power input and cleaning section, red represents the charging section, and green represents the power distribution section. Notice the red and blue bounding boxes both hold the LT3021 IC. This is because the LT3021 serves two purposes; cleaning the input power to some constant number and charging the batteries.

Power Input and Cleaning
The input power section is very repetitive. It uses the same circuit block 8 times, once for each solar panel input. Each block contains a current sensing IC and a diode to prevent energy flowing back to the solar panels. Power can flow back into panels when they are in shade, leading to loss. These current sensing ICs are part of the original design of the Inter Orbital board. They interface with a larger chip that was removed from the board. This chip was removed because software drivers could not be found to support it. The team decided that while it would have been beneficial for engineering data on the performance of the solar panels, it

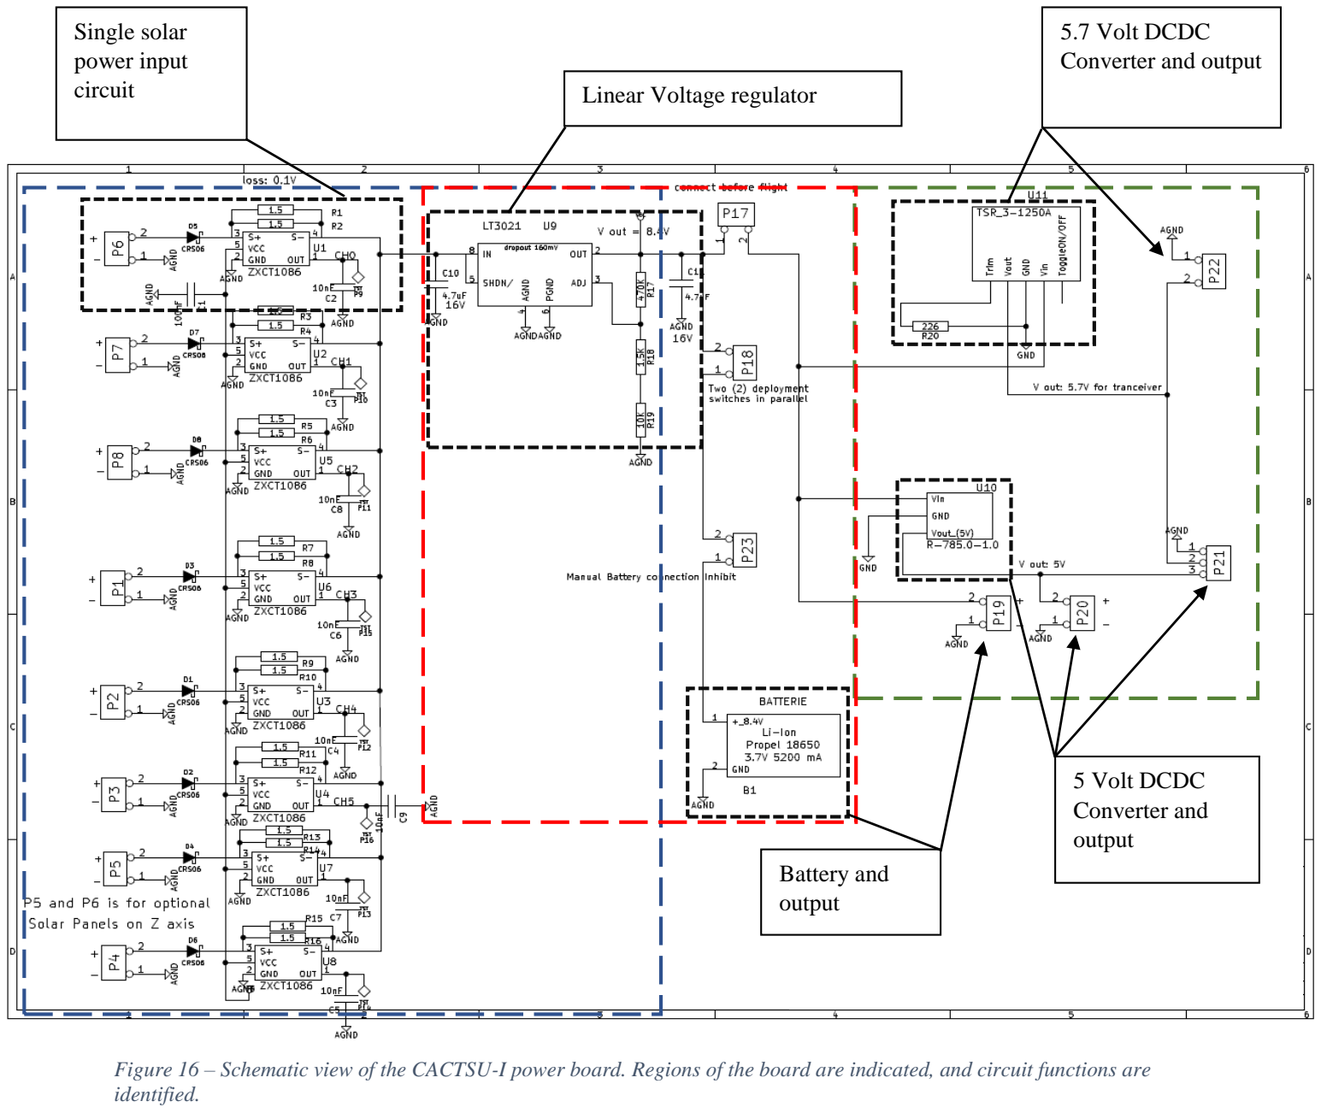
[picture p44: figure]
Single solar power input; circuit; Linear Voltage regulator; 5.7 Volt DCDC Converter and output; 5 Volt DCDC Converter and output; Battery and output; identified.

Figure 16 – Schematic view of the CACTSU-I power board. Regions of the board are indicated, and circuit functions are would not help the team or CubeSat make decisions during operation. There was no form of control over the solar panel inputs or the power distribution outputs.

The LT3021 IC is a voltage regulator and will now be referred to as the voltage regulator. The regulator is configured to regulate down to just under 8.4 volts, the final tuning was about 8.35 Volts but will be referred to as 8.4 volts. The reason this voltage regulator was configured to this voltage was to meet the max voltage of the Li-ion batteries used in CATUS-1. The solar panel voltage is nominally 13 volts, this ensures that the input voltage will always be regulated down to the max battery voltage. If the input voltage was lower than the regulator target voltage, the regulator would simply output that input voltage. This is the case with all linear voltage regulators, they only go from high voltages to lower voltages. Solar panels were designed with a higher peak voltage to combat degradation over time and imperfect pointing towards the sun.

Charging
The charging section is simply a connection to the batteries as the voltage regulator has already cleaned the input voltage to a stable 8.4 volts. The battery configuration for CACTUS-I is 2s2p. Two batteries in series, two sets in parallel. This configuration doubled the maximum and minimum voltage of the batteries and also doubled the potential current output. The battery voltage can change dramatically, especially in eclipse, because the configuration uses two batteries in series. The battery minimum voltage is 6 volts. This gives a total range of 2.4 volts. As the battery cycles between 25% and 75% DoD the voltage supply can change by upwards of a volt. This should not affect any components as the DCDC converters can accept this lower voltage and the voltage regulator will always regulate to 8.4 volts as it tries to charge the battery. Charging is done by holding a higher voltage potential to the batteries via the LT3021 voltage regulator so that charge always flow into the batteries. This flow will diminish as the difference between the current battery voltage and the max battery voltage decreases.

Power Distribution
The power distribution section was one of the section completely changed from the original design. While the original design did have a voltage boost circuit used to deliver the 5.7 volts needed for the communications board, during testing it was found to be unreliable. The IC used in the boost circuit would often overheat and burn out. This led to the removal of the boost circuit block and the addition of a simple DCDC converter. A DCDC converter was purchased instead of reworking the boost circuit to avoid more risk. The team was not comfortable with redesigning the boost circuit due to lack of experience and knowledge on the subject. The TSR 3-1250A DCDC Converter replaced the voltage boost circuit to supply the communication board. This converter was adjustable, so a trim resistor was used to supply the correct voltage to the communications board. The second DCDC converter, the R-785.0-1.0 was used to supply the 5 volts and 1 amp max to the Raspberry Pi 0. Both converters had lockout voltages below the minimum battery voltage. A lockout voltage is the lowest voltage a chip, DCDC converter, or other circuit can function at. Below the lockout voltage, the device will turn off. Having very low lockout voltages ensured that the DCDC converters would not suddenly turn off from the varying supply voltage.

Lessons Learned
Solar energy conversion inefficiencies will lead to more low power situations.

A linear regulator is used to convert the incoming solar energy to the proper bus voltage. Converting voltage will lead to some loss, though it can be small. In the case of a linear regulator the incoming voltage must be higher than the regulated voltage. The greater the difference between the incoming and regulated voltage the greater the inefficiency. The Solar panel voltage is estimated as 12.5 volts and the regulated voltage is 8.4 volts. To estimate the efficiency of the regulator a simple ratio can be used:

eff =

Vout

Vin

=

8.4
12.5

= 67.2%

An efficiency rating of 67.2 percent is poor compared to other converters with typical ratings between 85 and 95 percent. There are two ways to improve this efficiency, each with tradeoffs:

1. Remove one solar chip from a string to lower the overall voltage output of a solar panel by 2.5 Volts. Using the same equation above, this will result in an estimated efficiency of 84 percent, comparable to other DCDC converters. The benefits of this method are that it is low cost and the satellite will experience good efficiencies at beginning of life. The added risks with this method are a shorter satellite life time, and harder punishments from off pointing. The regulator will convert energy in a more efficient manner and this fix will not change any parts or increase costs. However, off pointing will cause the panel voltage to drop below the regulated voltage faster, making pointing errors more punishing. Panel degradation over time can reduce panel yield even further, worsening off pointing punishments. Recall that once the input voltage falls below the regulated the regulator will not work; it will simply pass the input voltage into the circuit.
2. Use a DCDC Converter in place of the voltage regulator. The added benefits are that voltages will be converted more efficiently and low voltages from off pointing can still be up converted, making for less loss. The downsides to this method is DCDC converters can be expensive and hard to find for the output voltage required. Voltages can be converted to the target voltage with efficiencies of 85 to 95 percent. Lower voltages can be up converted to reduce loss in a low yield situation, which is something a regulator cannot do. However, a voltage regulator with an output voltage target of 8.4 volts or 4.2 volts can be hard to find. This may be why the original design used a voltage regulator. Also, if a DCDC converter was found with the proper target voltage it could be very expensive.

Reduce risk of DCDC converter failure by adding input and output filters as well as protection diodes.

The DCDC converters used in the second rework of the power design worked during the many tests and Day in the Life tests ran. To ensure a long life add protection components to DCDC converters. These protections components will often be called out in part data sheets. The R-785.0-1.0 DCDC Converter will be used as an example. Below are two circuits with the R-785.0-1.0 converter and a form of protection. Figure 17 shows an optional diode that is used to prevent feedback current when a device is powered down. Feedback current could come from the device due to inductors storing current. The Raspberry Pi 0 used on CACTSU-I has a power inductor used to smoothen voltage transitions between 0 and 5 volts. This power conductors can be a source of current feedback. Option one can be used if the powered circuit (Raspberry Pi 0) is low in impedance, otherwise, option two should be used. To reduce electromagnetic noise a set of filters can be added to the input of the DCDC converter, shown in figure 18. While this is more important in lab applications with sensitive equipment, it of course can be argued that a CubeSat antenna operating near the noise floor is sensitive equipment. This is one way to reduce noise coming from the CubeSat itself.

Figure 17 – Optional protection diodes used to prevent damage to the DCDC converter from feedback current. A feedback can be experiences if a device is powered down and has inductors storing energy. Option 1 is a configuration to be used in the powered circuit is low in impedance, otherwise, option 2 should be used. Note that a output voltage reduction will be experienced

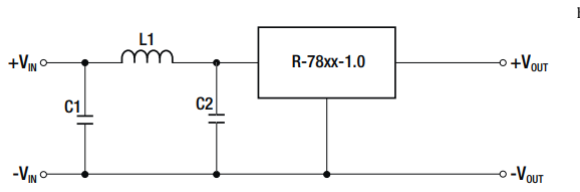
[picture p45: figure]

Initial fixation on finding a heritage design led to delays in the power board design being ready, leading to a rushed product.

During design, teams were guided to find an existing power board and adapt it to fit the needs of the CACTUS-I mission. Many power designs that were found did not have complete documentation or were far too complex for what was needed. Three main power board designs were looked at intently before arriving at the design that was used and modified. The reasoning behind not designing a power board in house was to make for an easier time defending the design in review. A heritage design that has flown before makes a much better stance than an unflown in-house design. This was done to also reduce risk to the system but unfortunately the design chosen was heavily modified to the point that creating a new design in-house would have been easier, cleaner, and have an equivalent outcome. Another part of the issue comes from the student body. No student on the CACTUS-I mission and not many students at Capitol were prepared to design a power board from scratch. This was another major factor that led to the decision of modifying an existing design and was extremely justified.

With the knowledge learned from this mission, a design should be created from scratch or a stricter set of requirements should be made and used to search for an existing design so that very little modification is needed.
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

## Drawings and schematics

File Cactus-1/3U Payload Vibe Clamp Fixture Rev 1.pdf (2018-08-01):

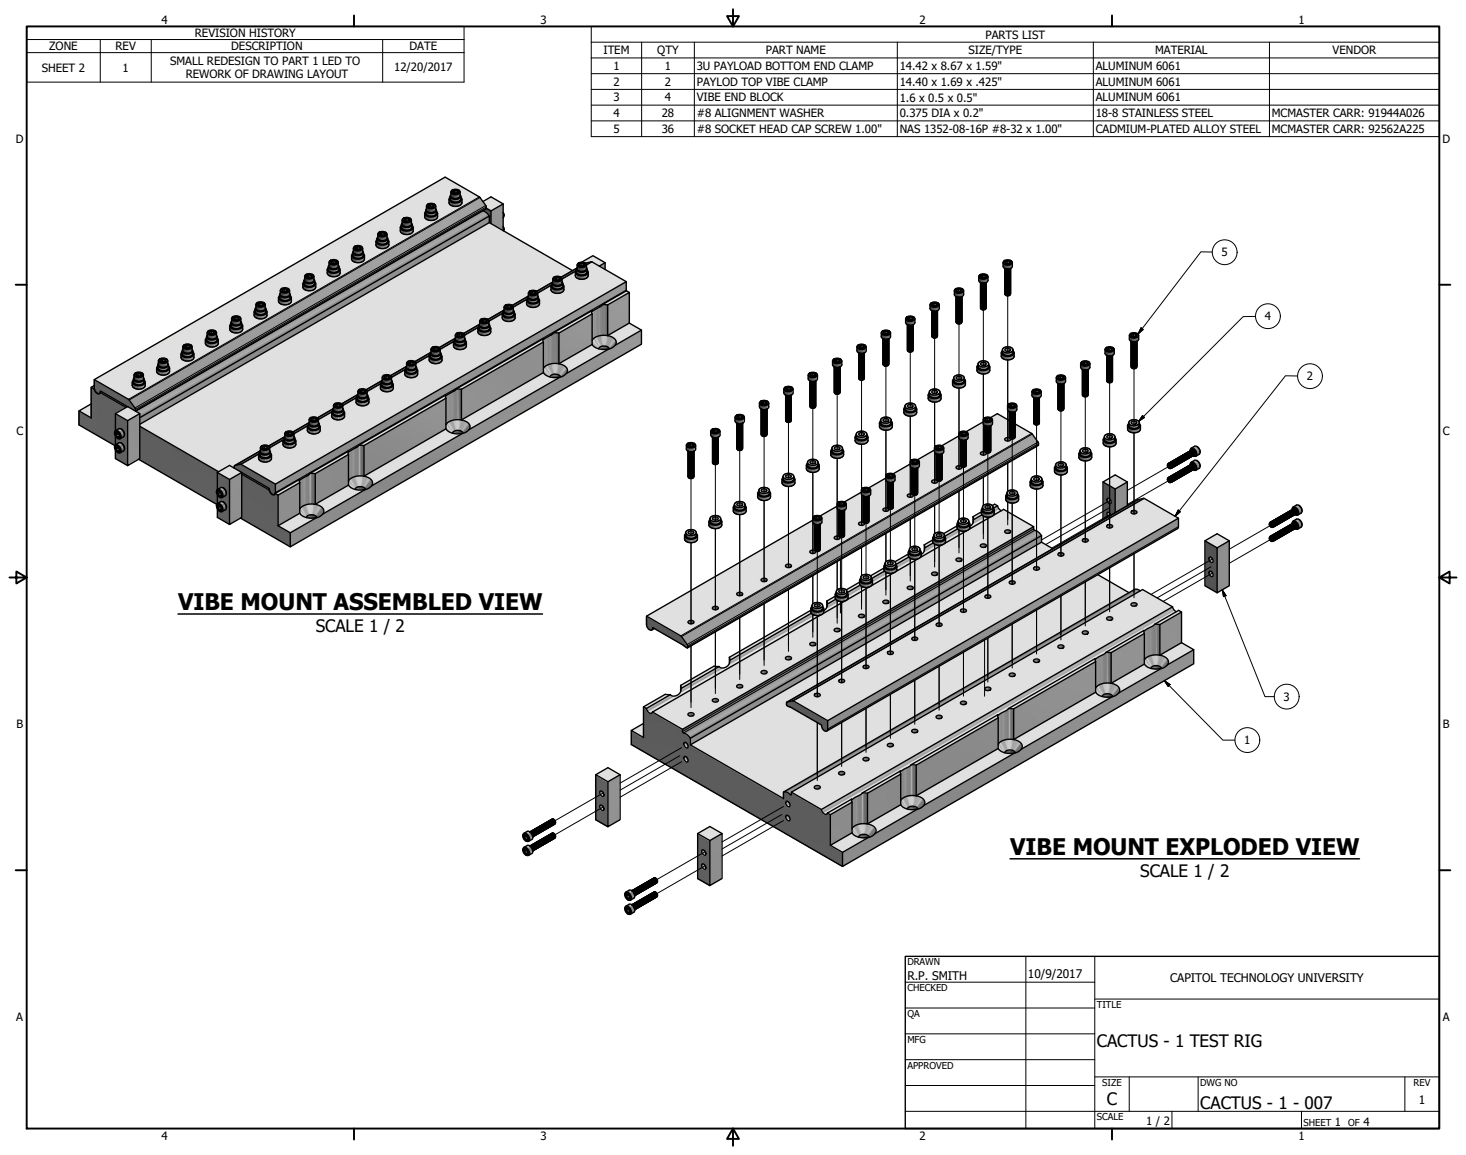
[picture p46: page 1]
SCALE 1 / 2; PARTS LIST; ITEM; QTY; PART NAME; SIZE/TYPE; MATERIAL; VENDOR; 3U PAYLOAD BOTTOM END CLAMP; ALUMINUM 6061; PAYLOD TOP VIBE CLAMP; VIBE END BLOCK; #8 ALIGNMENT WASHER; 0.375 DIA x 0.2"; 18-8 STAINLESS STEEL; MCMASTER CARR: 91944A026; #8 SOCKET HEAD CAP SCREW 1.00"; NAS 1352-08-16P #8-32 x 1.00"; CADMIUM-PLATED ALLOY STEEL MCMASTER CARR: 92562A225; SHEET 1 OF 4; DRAWN; CHECKED; MFG; APPROVED; R.P. SMITH; DWG NO CACTUS - 1 - 007; TITLE; SIZE C; SCALE; REV; REVISION HISTORY; ZONE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

SMALL REDESIGN TO PART 1 LED TO
REWORK OF DRAWING LAYOUT

VIBE MOUNT ASSEMBLED VIEW

VIBE MOUNT EXPLODED VIEW

CAPITOL TECHNOLOGY UNIVERSITY

CACTUS - 1 TEST RIG

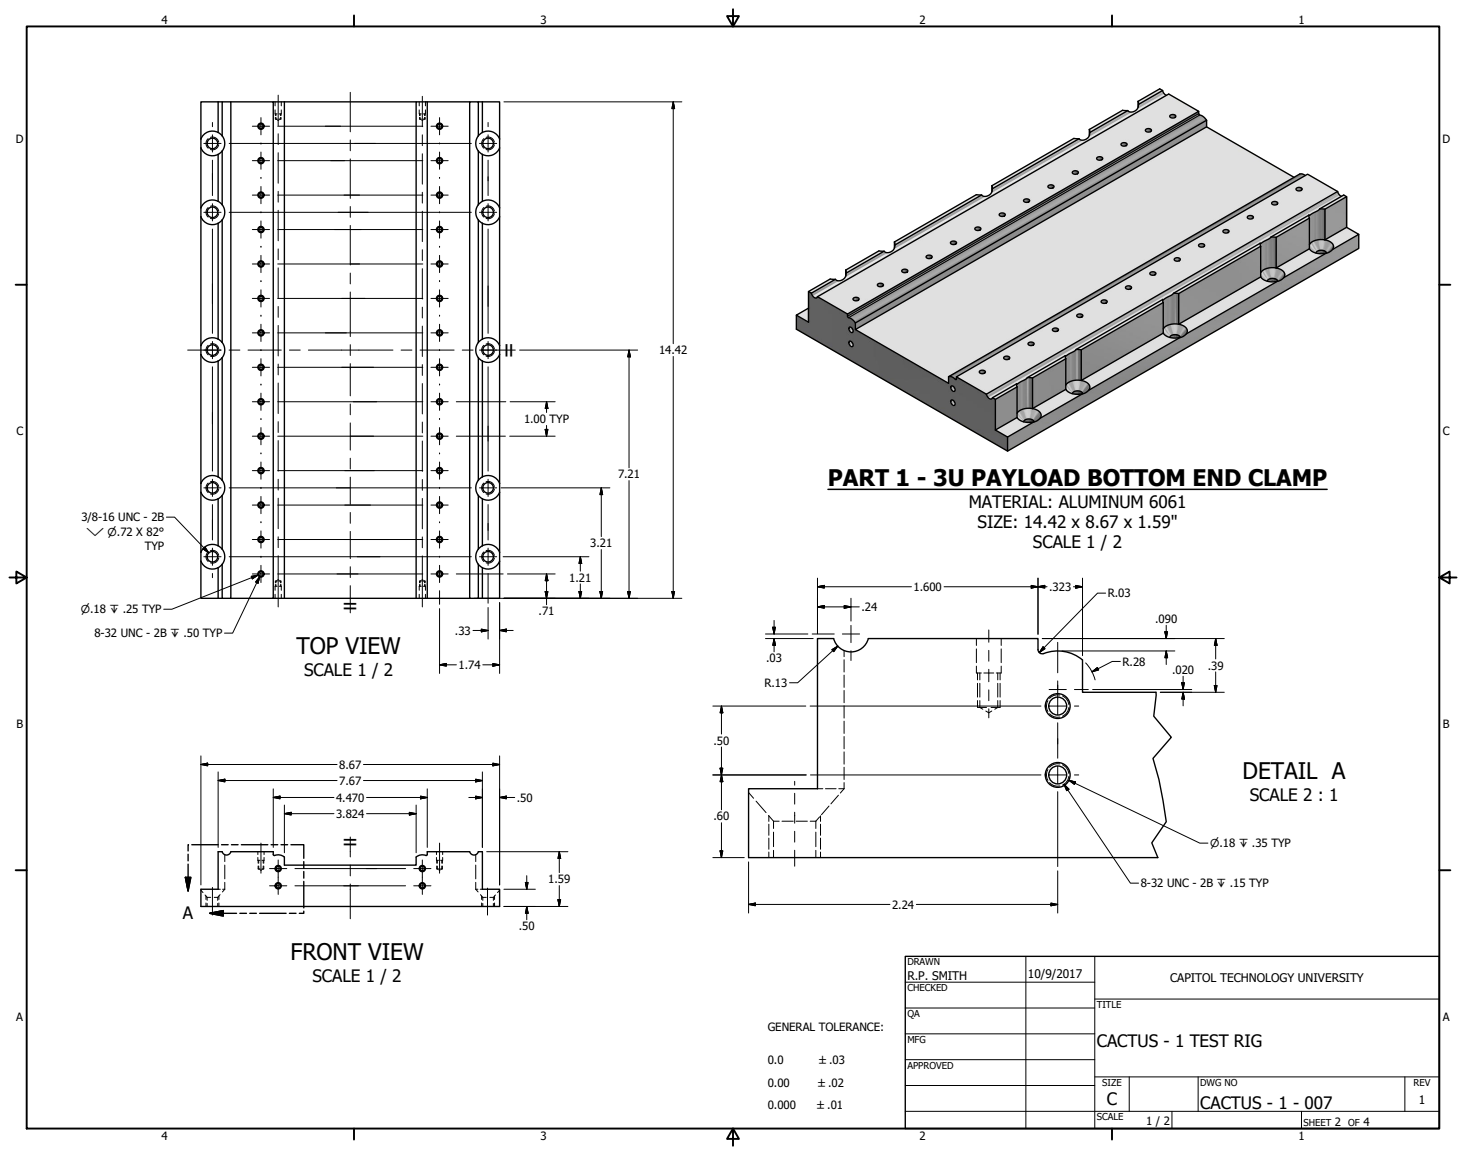
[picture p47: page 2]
TOP VIEW; SCALE 1 / 2; FRONT VIEW; MATERIAL: ALUMINUM 6061 SIZE: 14.42 x 8.67 x 1.59" SCALE 1 / 2; DETAIL A; SCALE 2 : 1; DRAWN; CHECKED; MFG; R.P. SMITH; TITLE; GENERAL TOLERANCE:; P.18 Z .35 TYP; 1.00 TYP; P.18 Z .25 TYP; 8-32 UNC - 2B Z .50 TYP; 3/8-16 UNC - 2B Y P.72 X 82°; TYP; 8-32 UNC - 2B Z .15 TYP

PART 1 - 3U PAYLOAD BOTTOM END CLAMP

CAPITOL TECHNOLOGY UNIVERSITY

CACTUS - 1 TEST RIG

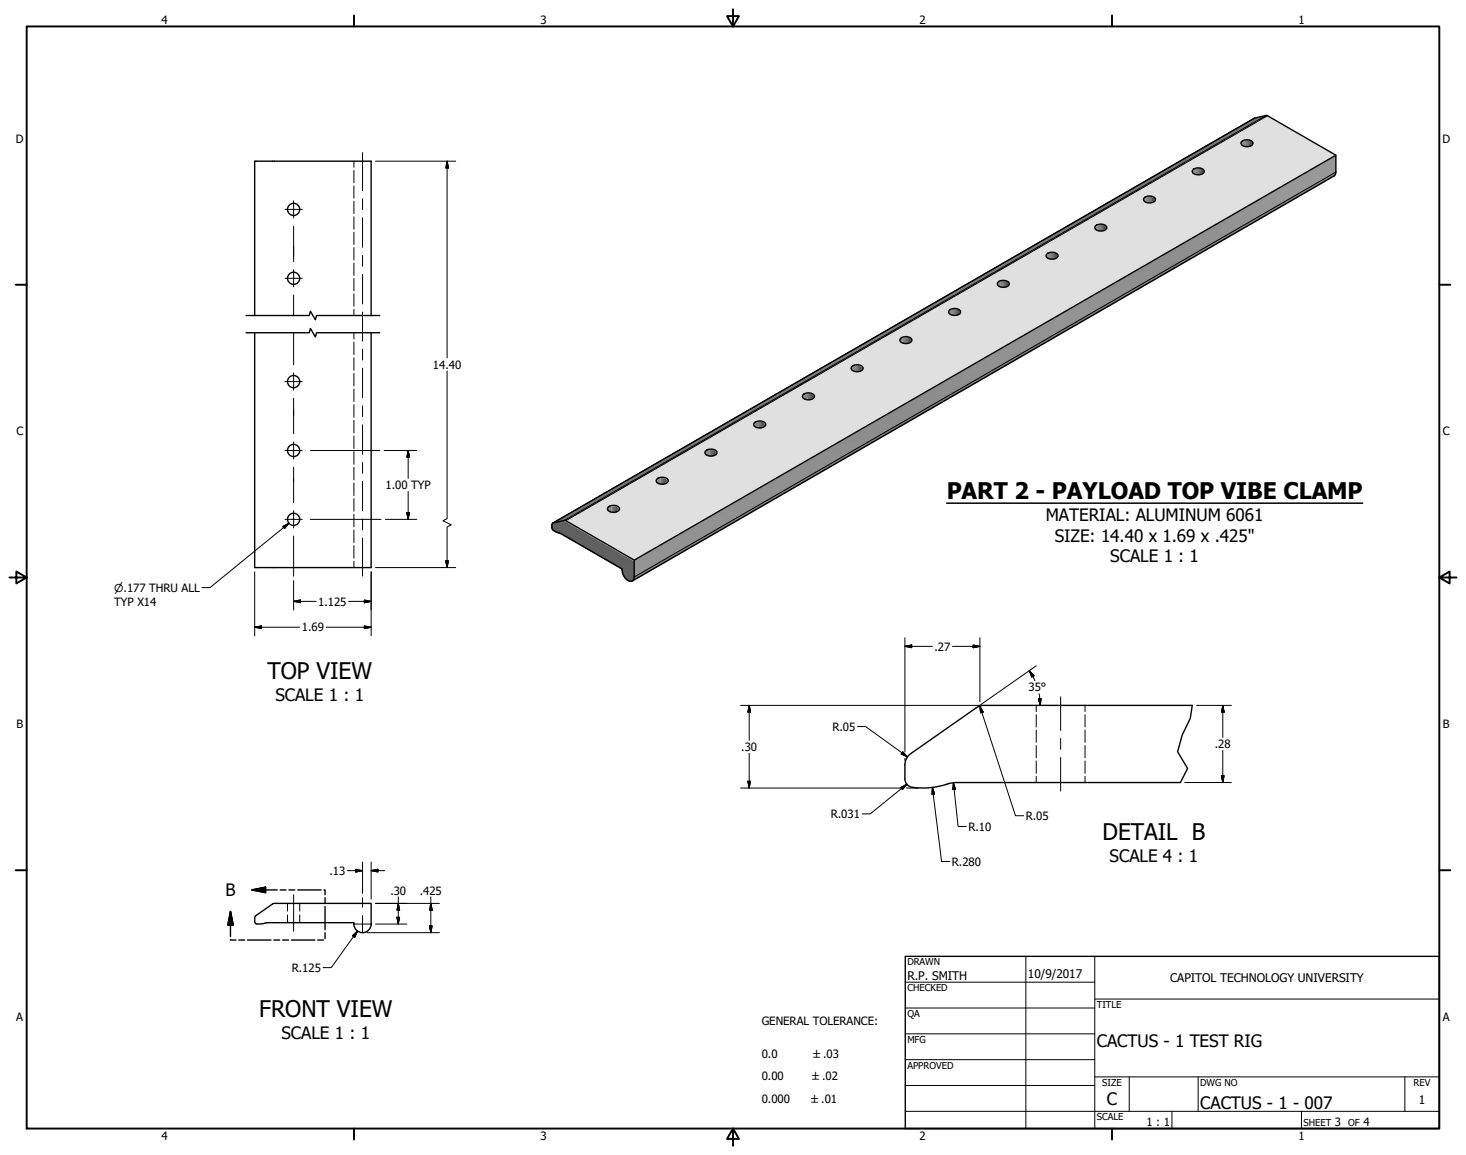
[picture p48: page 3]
FRONT VIEW; SCALE 1 : 1; TOP VIEW; DETAIL B; SCALE 4 : 1; MATERIAL: ALUMINUM 6061 SIZE: 14.40 x 1.69 x .425" SCALE 1 : 1; DRAWN; CHECKED; MFG; R.P. SMITH; TITLE; 1.00 TYP; P.177 THRU ALL; TYP X14; GENERAL TOLERANCE:

PART 2 - PAYLOAD TOP VIBE CLAMP

CAPITOL TECHNOLOGY UNIVERSITY

CACTUS - 1 TEST RIG

=

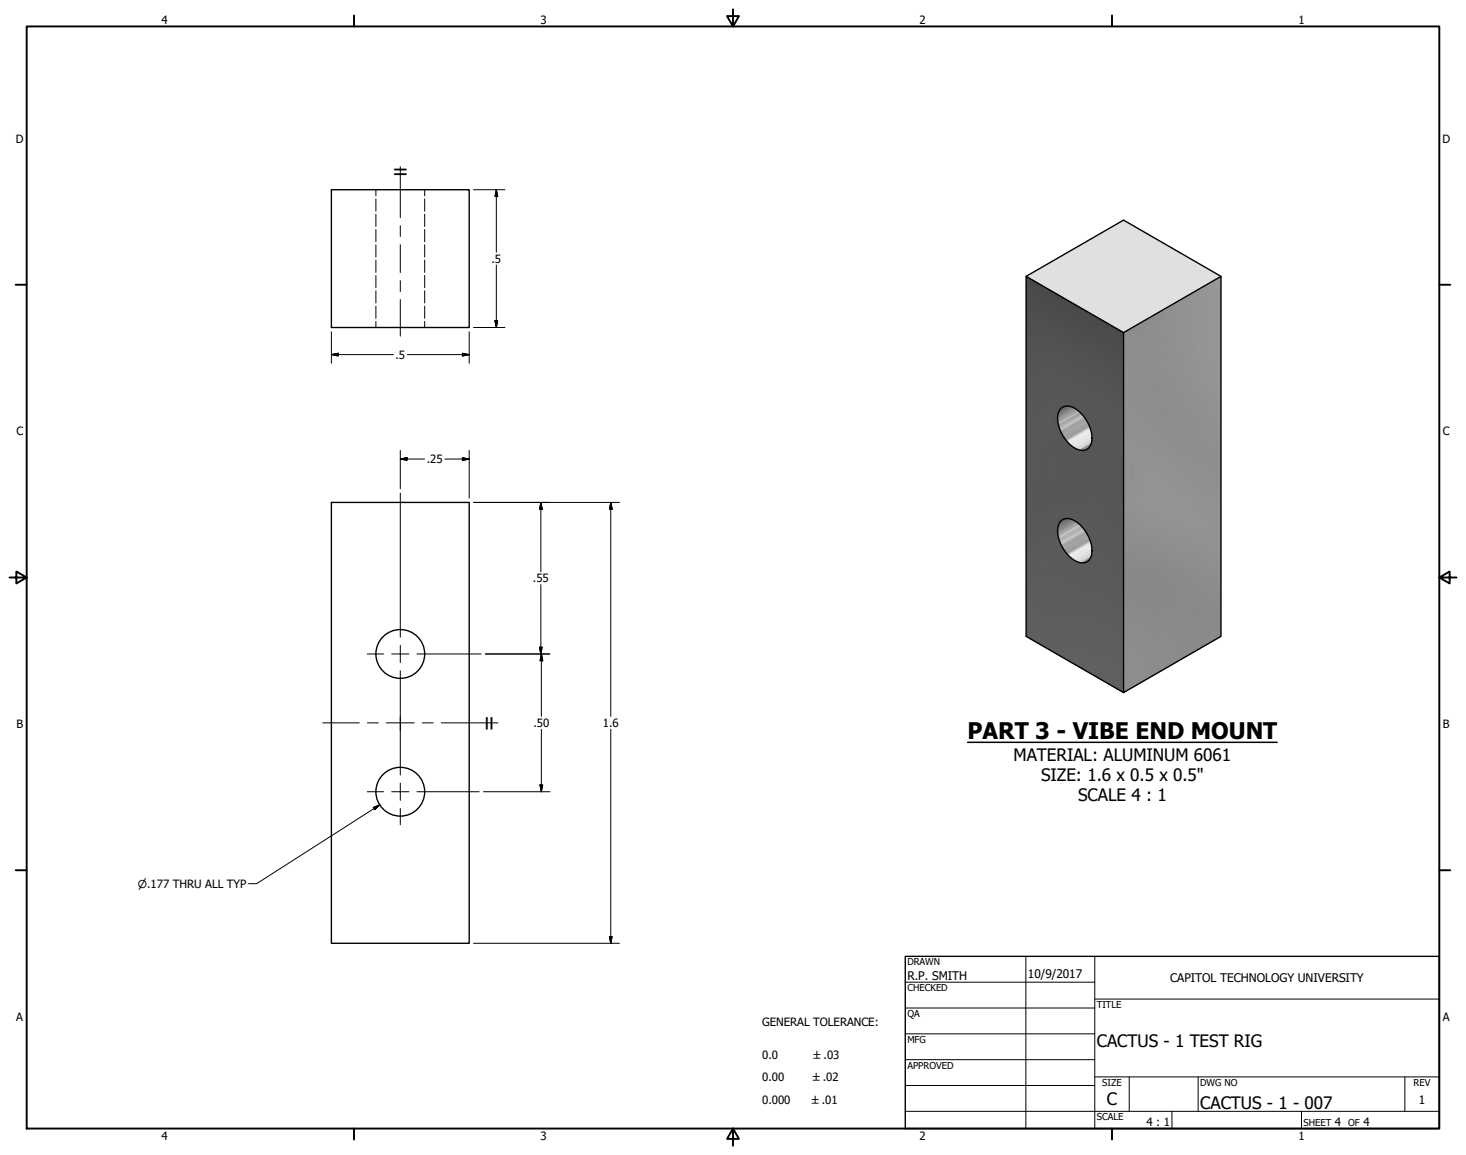
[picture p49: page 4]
DRAWN; CHECKED; MFG; R.P. SMITH; TITLE; GENERAL TOLERANCE:

PART 3 - VIBE END MOUNT
MATERIAL: ALUMINUM 6061
SIZE: 1.6 x 0.5 x 0.5"
SCALE 4 : 1

P.177 THRU ALL TYP

CAPITOL TECHNOLOGY UNIVERSITY

CACTUS - 1 TEST RIG

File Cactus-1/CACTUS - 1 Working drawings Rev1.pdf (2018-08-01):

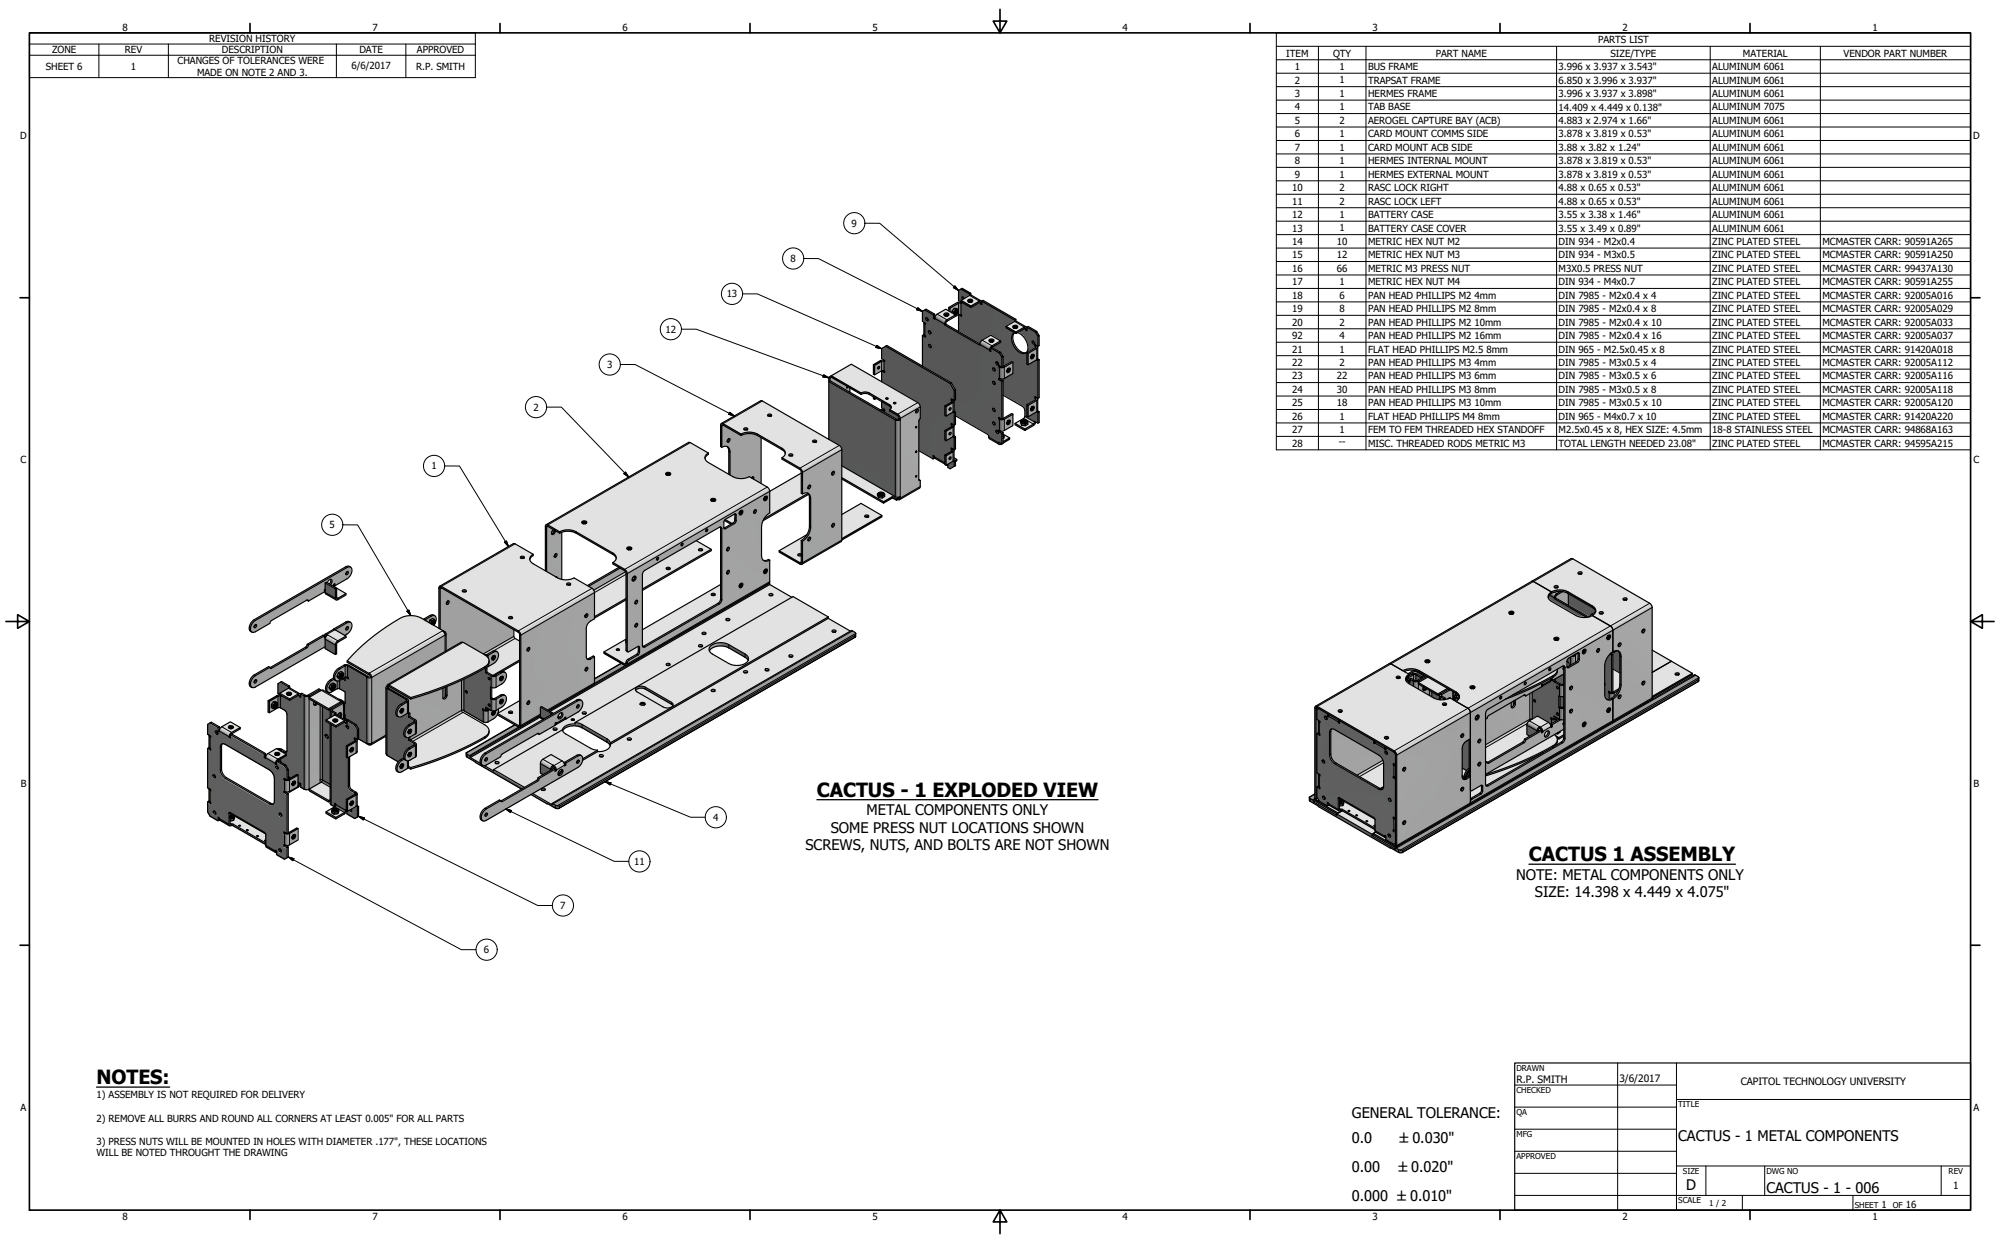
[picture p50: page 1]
PARTS LIST; ITEM; QTY; PART NAME; SIZE/TYPE; MATERIAL; VENDOR PART NUMBER; BUS FRAME; ALUMINUM 6061; TRAPSAT FRAME; HERMES FRAME; TAB BASE; ALUMINUM 7075; AEROGEL CAPTURE BAY (ACB); CARD MOUNT COMMS SIDE; CARD MOUNT ACB SIDE; HERMES INTERNAL MOUNT; HERMES EXTERNAL MOUNT; RASC LOCK RIGHT; RASC LOCK LEFT; BATTERY CASE; BATTERY CASE COVER; METRIC HEX NUT M2; DIN 934 - M2x0.4; ZINC PLATED STEEL; MCMASTER CARR: 90591A265; METRIC HEX NUT M3; DIN 934 - M3x0.5; MCMASTER CARR: 90591A250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

CHANGES OF TOLERANCES WERE
MADE ON NOTE 2 AND 3.

CACTUS - 1 EXPLODED VIEW

METAL COMPONENTS ONLY
SOME PRESS NUT LOCATIONS SHOWN
SCREWS, NUTS, AND BOLTS ARE NOT SHOWN

CACTUS 1 ASSEMBLY
NOTE: METAL COMPONENTS ONLY
SIZE: 14.398 x 4.449 x 4.075"

CAPITOL TECHNOLOGY UNIVERSITY

1) ASSEMBLY IS NOT REQUIRED FOR DELIVERY

2) REMOVE ALL BURRS AND ROUND ALL CORNERS AT LEAST 0.005" FOR ALL PARTS

CACTUS - 1 METAL COMPONENTS

3) PRESS NUTS WILL BE MOUNTED IN HOLES WITH DIAMETER .177", THESE LOCATIONS
WILL BE NOTED THROUGHT THE DRAWING

# BACK VIEW

## SCALE 1 : 1

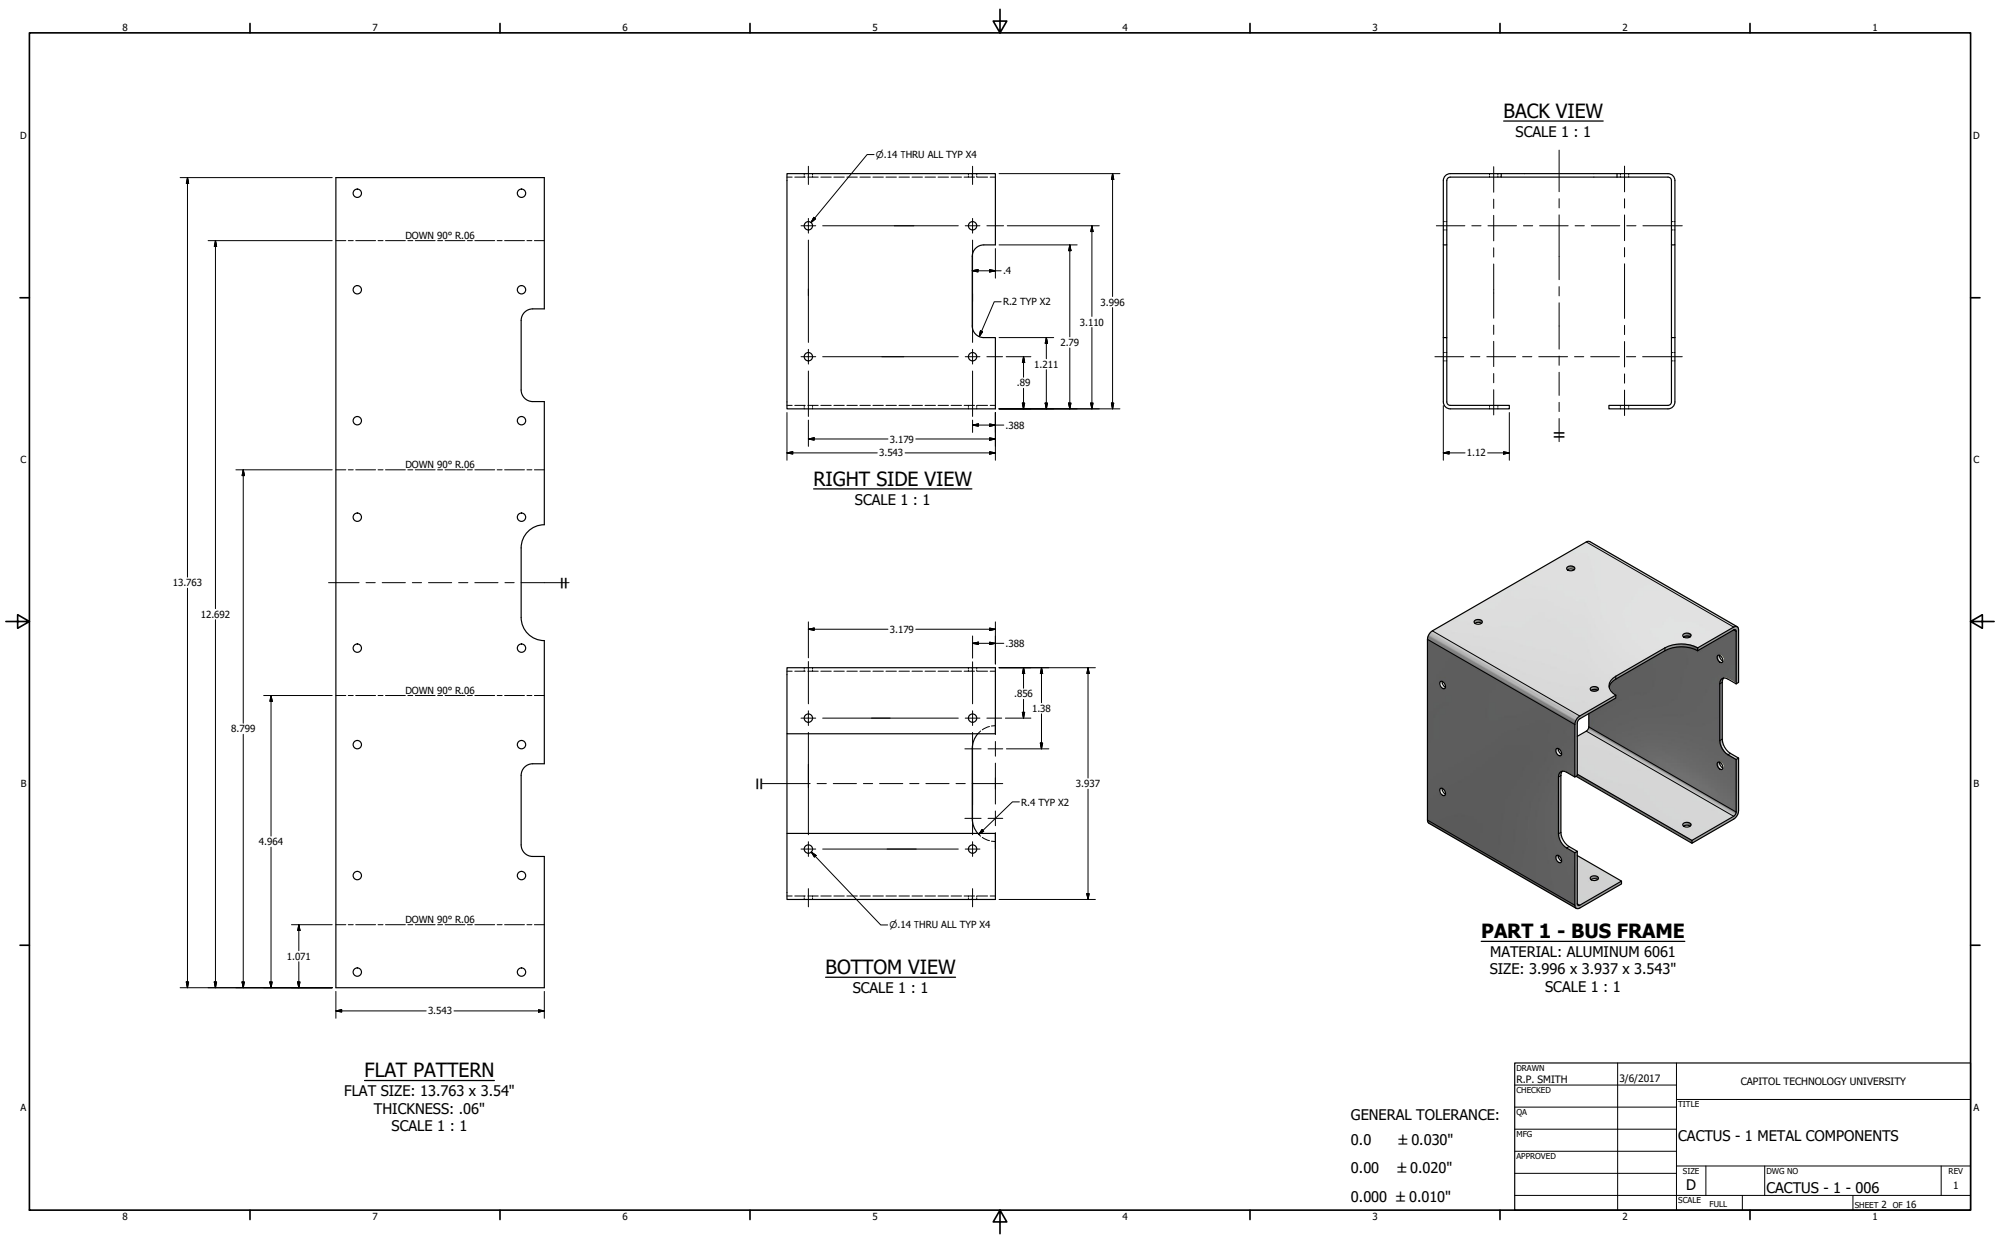
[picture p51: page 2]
FLAT PATTERN; FLAT SIZE: 13.763 x 3.54" THICKNESS: .06" SCALE 1 : 1; SCALE 1 : 1; BOTTOM VIEW; DRAWN; CHECKED; MFG; R.P. SMITH; TITLE; DOWN 90° R.06; R.4 TYP X2; R.2 TYP X2; P.14 6HRU ALL TYP X4; GENERAL TOLERANCE:; FULL

RIGHT SIDE VIEW
SCALE 1 : 1

PART 1 - BUS FRAME
MATERIAL: ALUMINUM 6061
SIZE: 3.996 x 3.937 x 3.543"

CAPITOL TECHNOLOGY UNIVERSITY

CACTUS - 1 METAL COMPONENTS

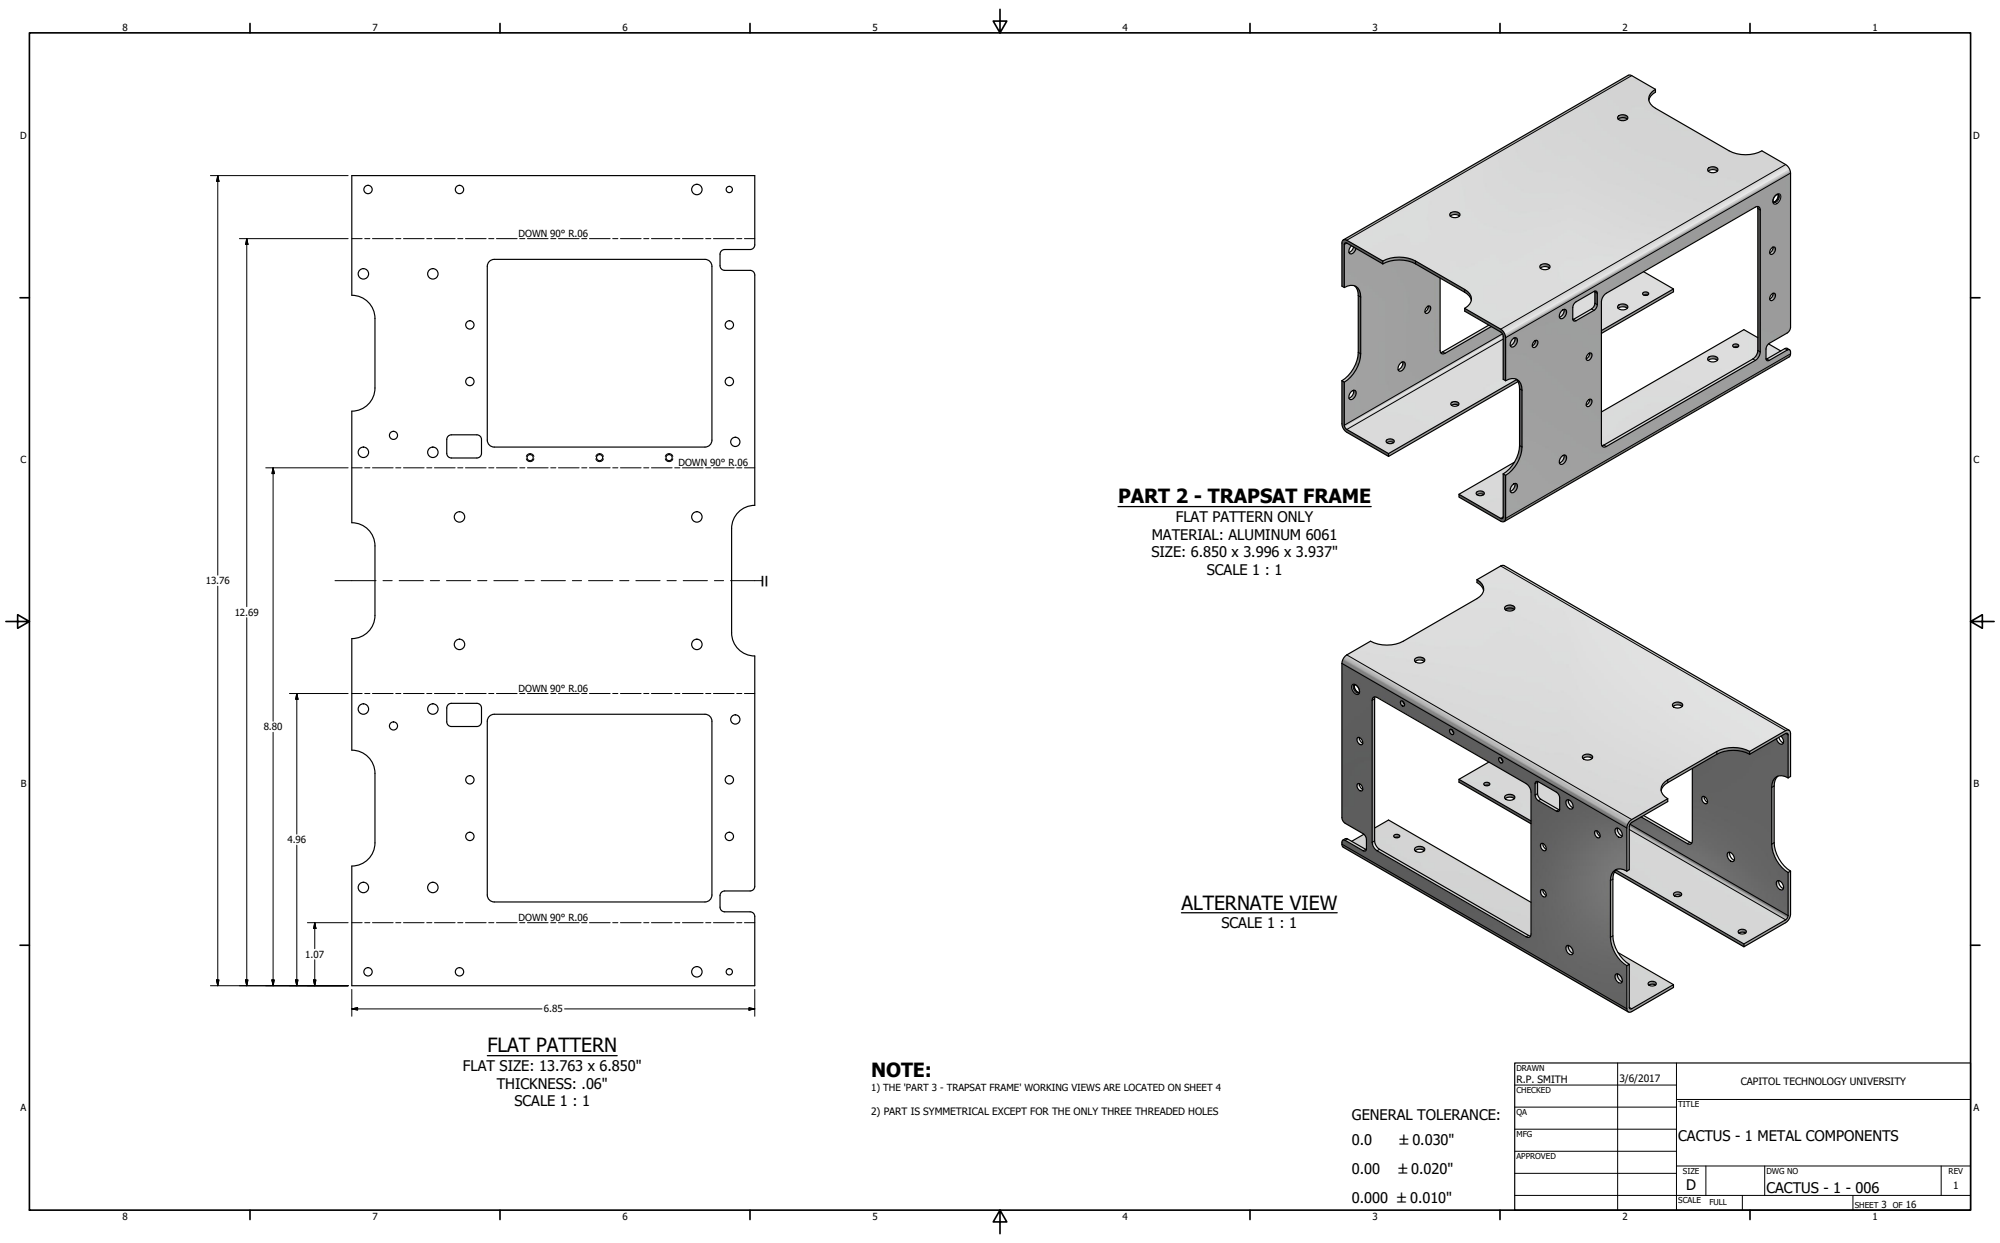
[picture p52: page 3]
FLAT PATTERN; FLAT SIZE: 13.763 x 6.850" THICKNESS: .06" SCALE 1 : 1; SCALE 1 : 1; ALTERNATE VIEW; DRAWN; CHECKED; MFG; R.P. SMITH; TITLE; GENERAL TOLERANCE:; NOTE:; DOWN 90° R.06; FULL

PART 2 - TRAPSAT FRAME

FLAT PATTERN ONLY
MATERIAL: ALUMINUM 6061
SIZE: 6.850 x 3.996 x 3.937"

CAPITOL TECHNOLOGY UNIVERSITY

1) THE 'PART 3 - TRAPSAT FRAME' WORKING VIEWS ARE LOCATED ON SHEET 4

2) PART IS SYMMETRICAL EXCEPT FOR THE ONLY THREE THREADED HOLES

CACTUS - 1 METAL COMPONENTS

# NOTE:

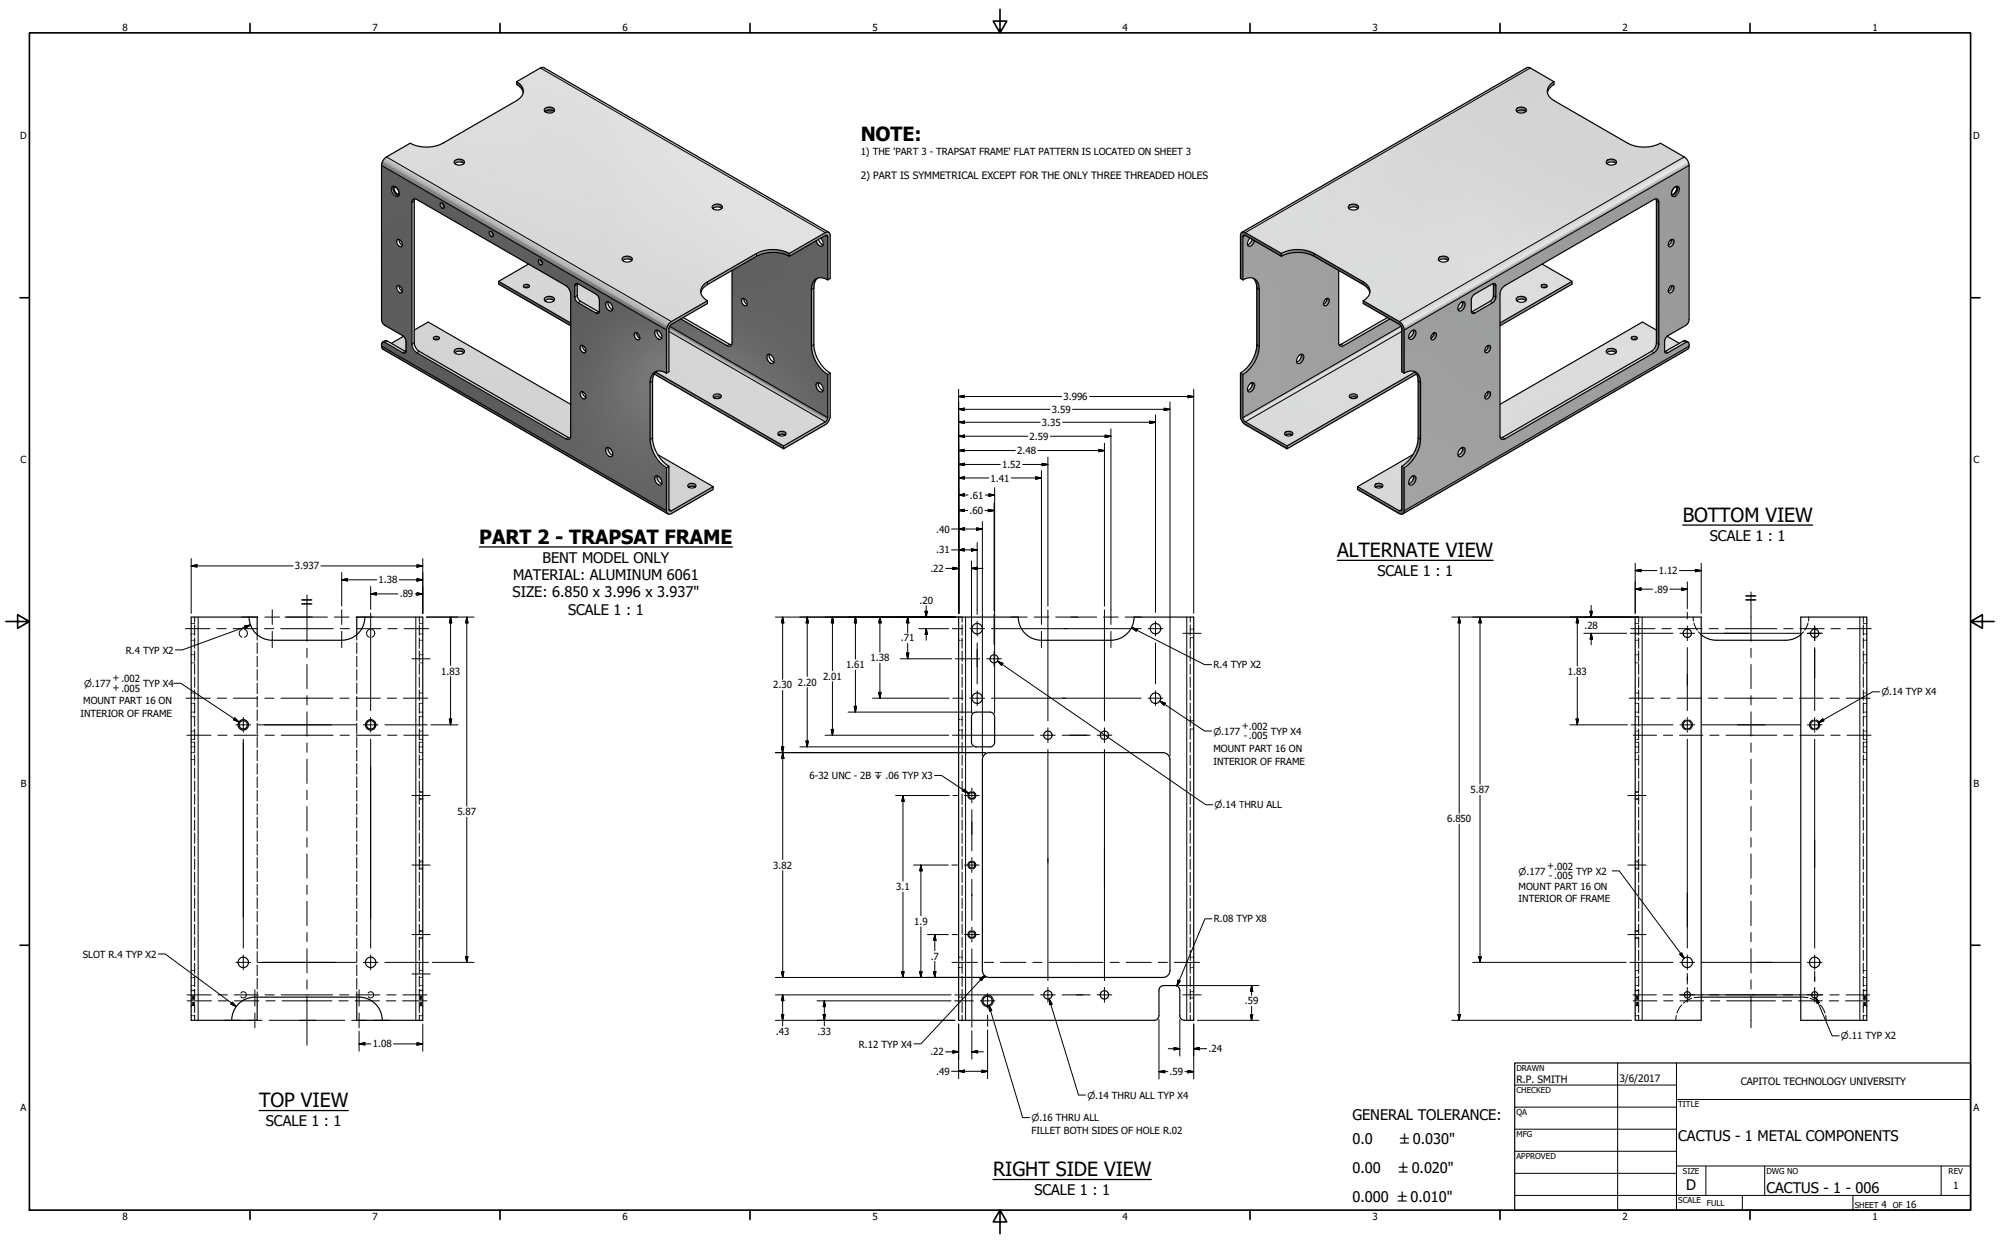
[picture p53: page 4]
SCALE 1 : 1; TOP VIEW; BOTTOM VIEW; ALTERNATE VIEW; DRAWN; CHECKED; MFG; R.P. SMITH; TITLE; SLOT R.4 TYP X2; R.4 TYP X2; TYP X4; GENERAL TOLERANCE:; P.14 6HRU ALL; R.12 TYP X4; P.14 TYP X4; TYP X2; P.11 TYP X2; 6-32 UNC - 2B Z .06 TYP X3; R.08 TYP X8; FULL

1) THE 'PART 3 - TRAPSAT FRAME' FLAT PATTERN IS LOCATED ON SHEET 3

2) PART IS SYMMETRICAL EXCEPT FOR THE ONLY THREE THREADED HOLES

PART 2 - TRAPSAT FRAME

BENT MODEL ONLY
MATERIAL: ALUMINUM 6061
SIZE: 6.850 x 3.996 x 3.937"

MOUNT PART 16 ON
INTERIOR OF FRAME

CAPITOL TECHNOLOGY UNIVERSITY

P.14 THRU ALL TYP X4

P.16 THRU ALL
FILLET BOTH SIDES OF HOLE R.02
RIGHT SIDE VIEW
SCALE 1 : 1

CACTUS - 1 METAL COMPONENTS

# TOP VIEW

## SCALE 1 : 1

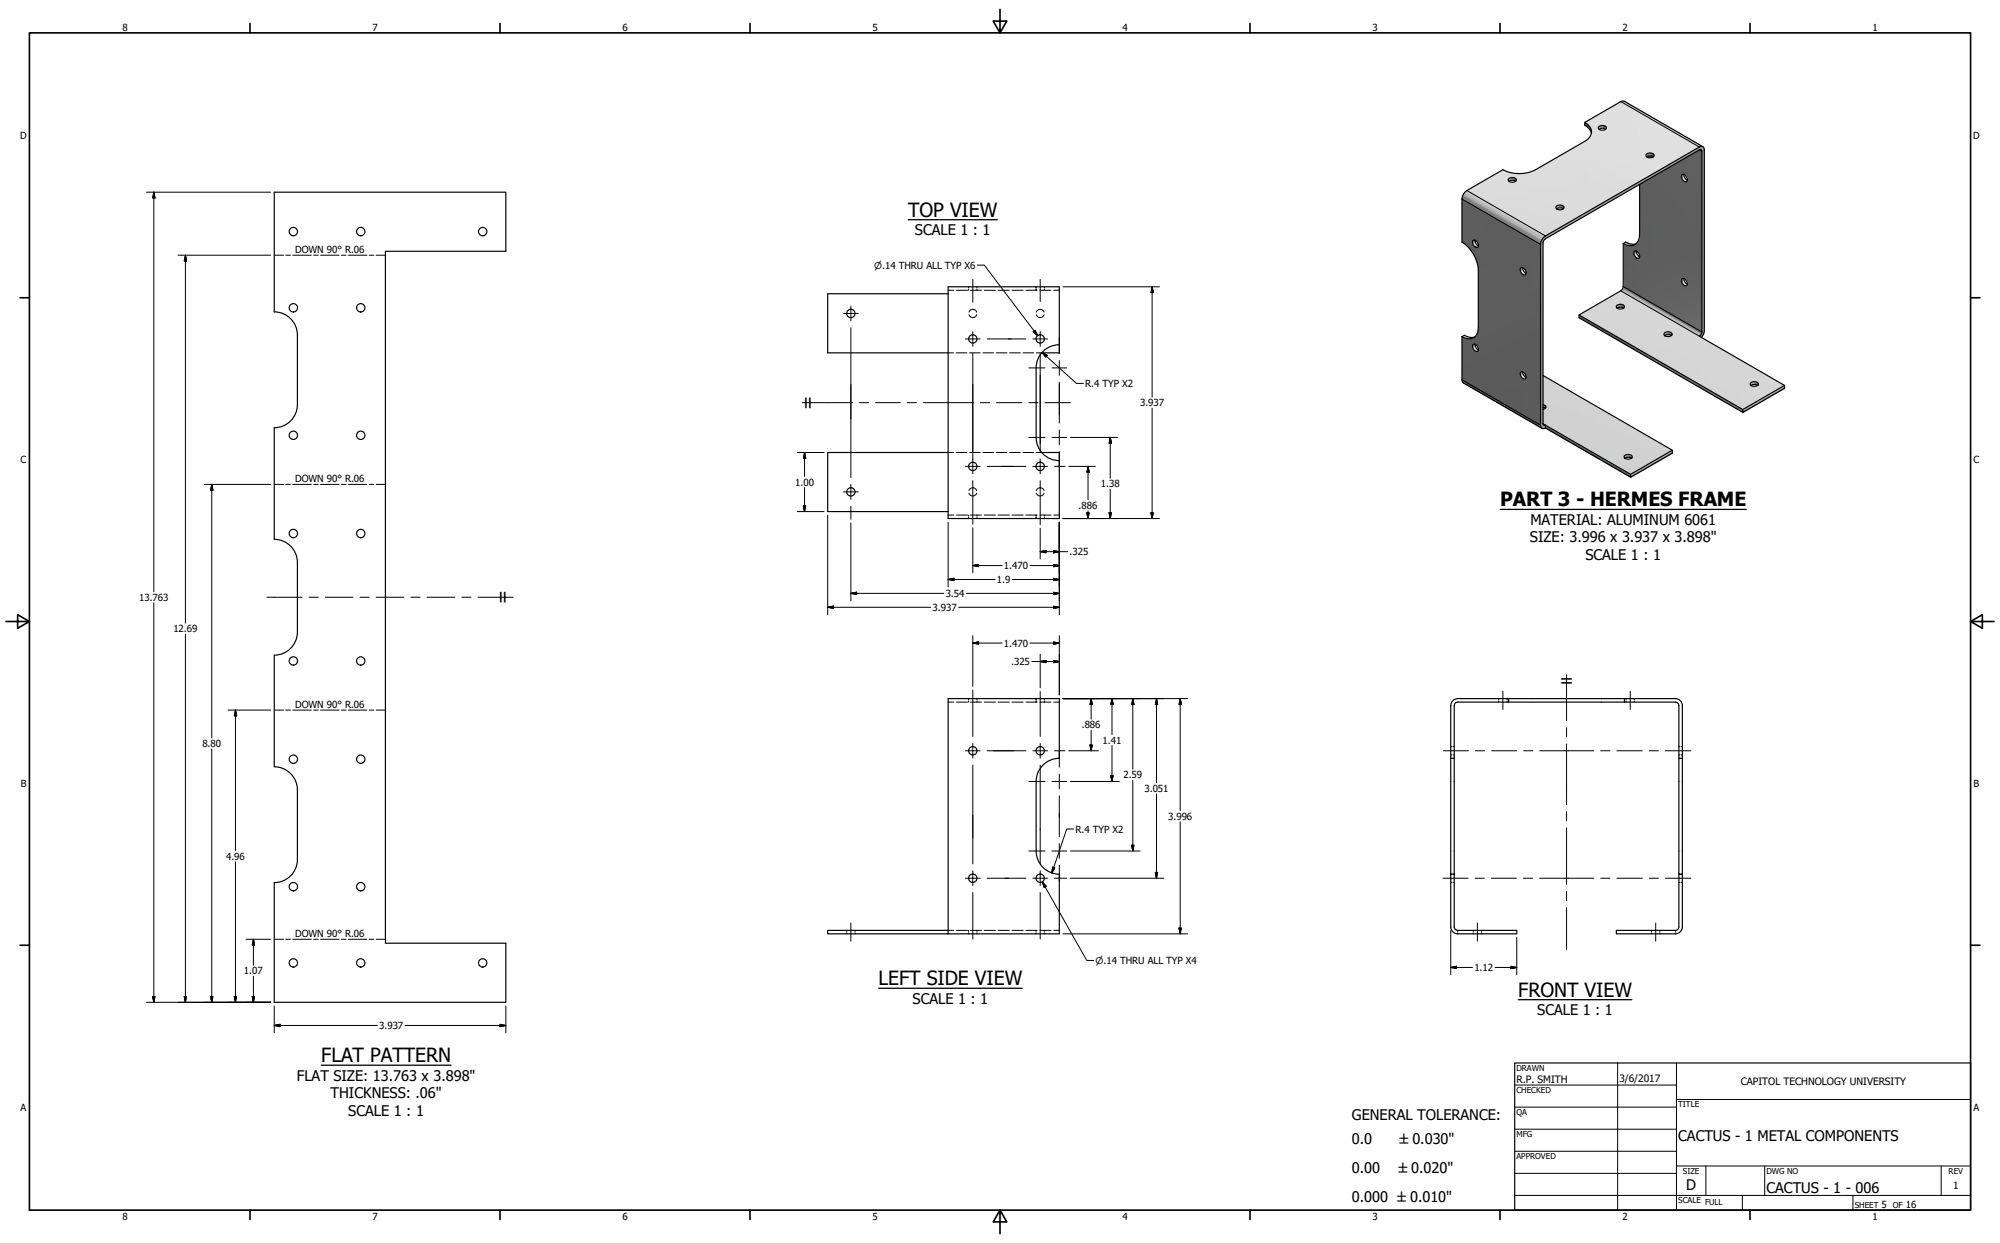
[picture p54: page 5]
FLAT PATTERN; FLAT SIZE: 13.763 x 3.898" THICKNESS: .06" SCALE 1 : 1; FRONT VIEW; SCALE 1 : 1; DRAWN; CHECKED; MFG; R.P. SMITH; TITLE; DOWN 90° R.06; R.4 TYP X2; GENERAL TOLERANCE:; FULL

P.14 THRU ALL TYP X6

PART 3 - HERMES FRAME
MATERIAL: ALUMINUM 6061
SIZE: 3.996 x 3.937 x 3.898"

P.14 THRU ALL TYP X4

LEFT SIDE VIEW
SCALE 1 : 1

CAPITOL TECHNOLOGY UNIVERSITY

CACTUS - 1 METAL COMPONENTS

# TOP VIEW

## SCALE 1 : 1

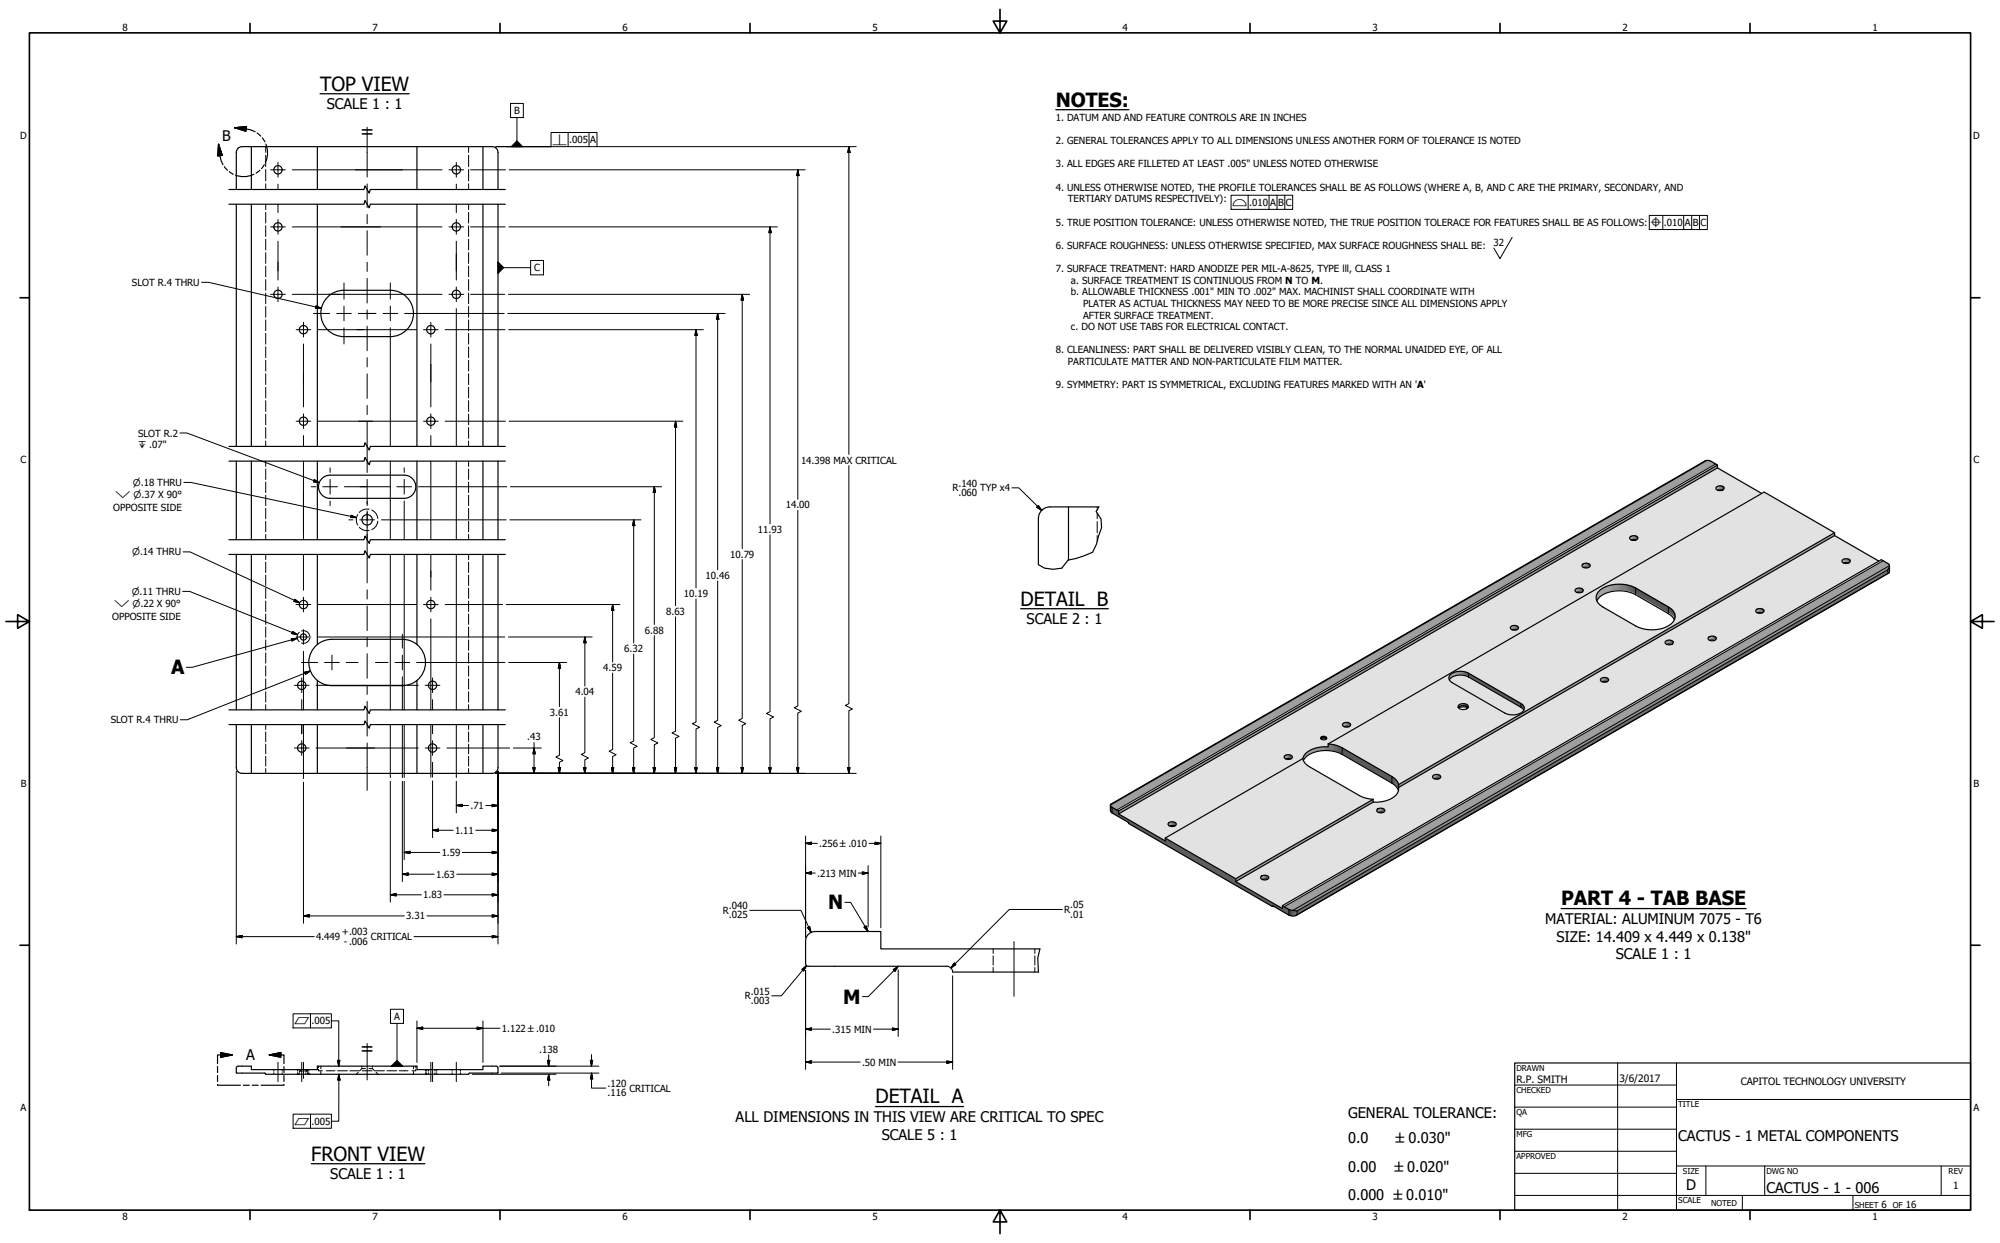
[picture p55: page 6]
SCALE 1 : 1; FRONT VIEW; DETAIL A; SCALE 5 : 1; DETAIL B; SCALE 2 : 1; DRAWN; CHECKED; MFG; R.P. SMITH; TITLE; NOTES:; CRITICAL; TYP x4; .315 MIN; .213 MIN; 14.398 MAX CRITICAL; .50 MIN; NOTED; SLOT R.4 THRU; SLOT R.2 Z .07"; P.14 THRU; P.11 THRU Y P.22 X 90°; OPPOSITE SIDE; P.18 THRU Y P.37 X 90°; GENERAL TOLERANCE:

1. DATUM AND AND FEATURE CONTROLS ARE IN INCHES

2. GENERAL TOLERANCES APPLY TO ALL DIMENSIONS UNLESS ANOTHER FORM OF TOLERANCE IS NOTED

3. ALL EDGES ARE FILLETED AT LEAST .005" UNLESS NOTED OTHERWISE

4. UNLESS OTHERWISE NOTED, THE PROFILE TOLERANCES SHALL BE AS FOLLOWS (WHERE A, B, AND C ARE THE PRIMARY, SECONDARY, AND
TERTIARY DATUMS RESPECTIVELY):

5. TRUE POSITION TOLERANCE: UNLESS OTHERWISE NOTED, THE TRUE POSITION TOLERACE FOR FEATURES SHALL BE AS FOLLOWS:

6. SURFACE ROUGHNESS: UNLESS OTHERWISE SPECIFIED, MAX SURFACE ROUGHNESS SHALL BE:

7. SURFACE TREATMENT: HARD ANODIZE PER MIL-A-8625, TYPE lll, CLASS 1
a. SURFACE TREATMENT IS CONTINUOUS FROM N TO M.
b. ALLOWABLE THICKNESS .001" MIN TO .002" MAX. MACHINIST SHALL COORDINATE WITH
PLATER AS ACTUAL THICKNESS MAY NEED TO BE MORE PRECISE SINCE ALL DIMENSIONS APPLY
AFTER SURFACE TREATMENT.
c. DO NOT USE TABS FOR ELECTRICAL CONTACT.
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

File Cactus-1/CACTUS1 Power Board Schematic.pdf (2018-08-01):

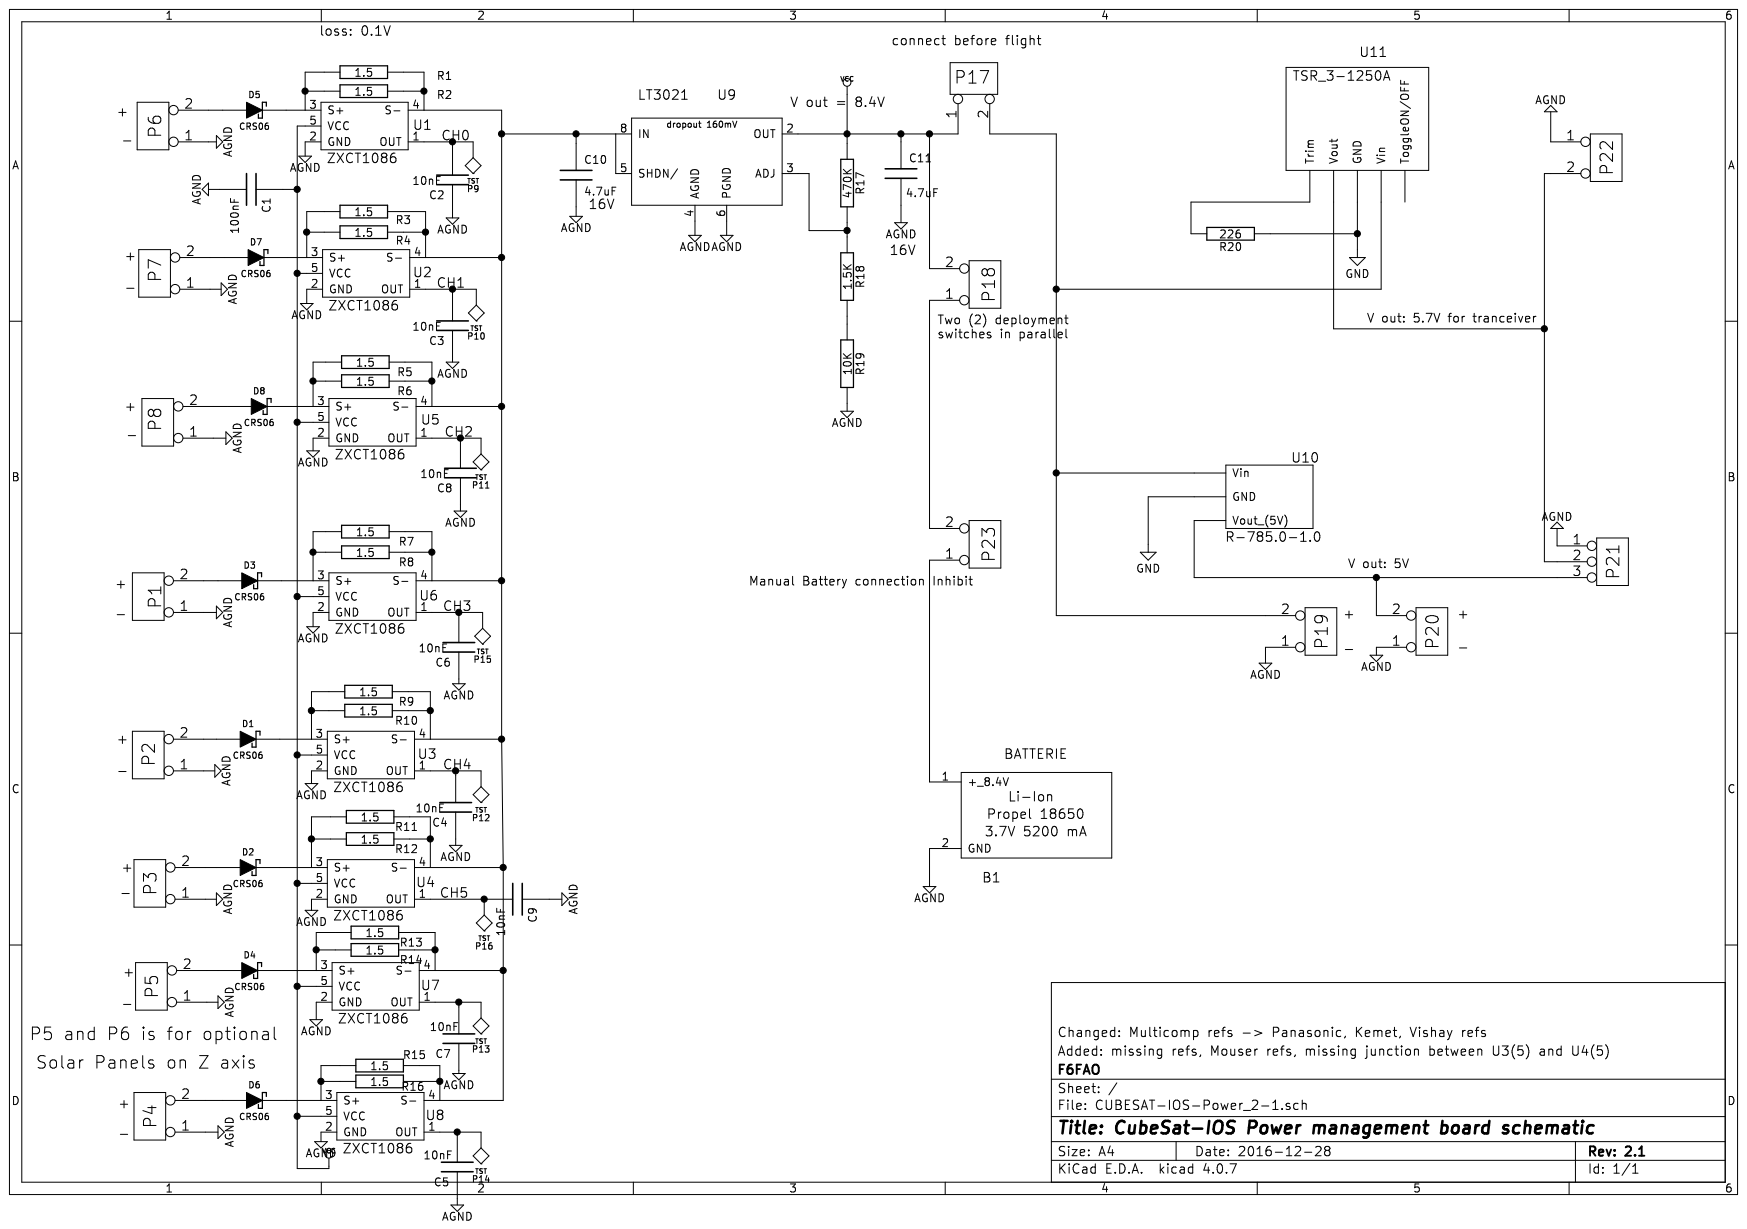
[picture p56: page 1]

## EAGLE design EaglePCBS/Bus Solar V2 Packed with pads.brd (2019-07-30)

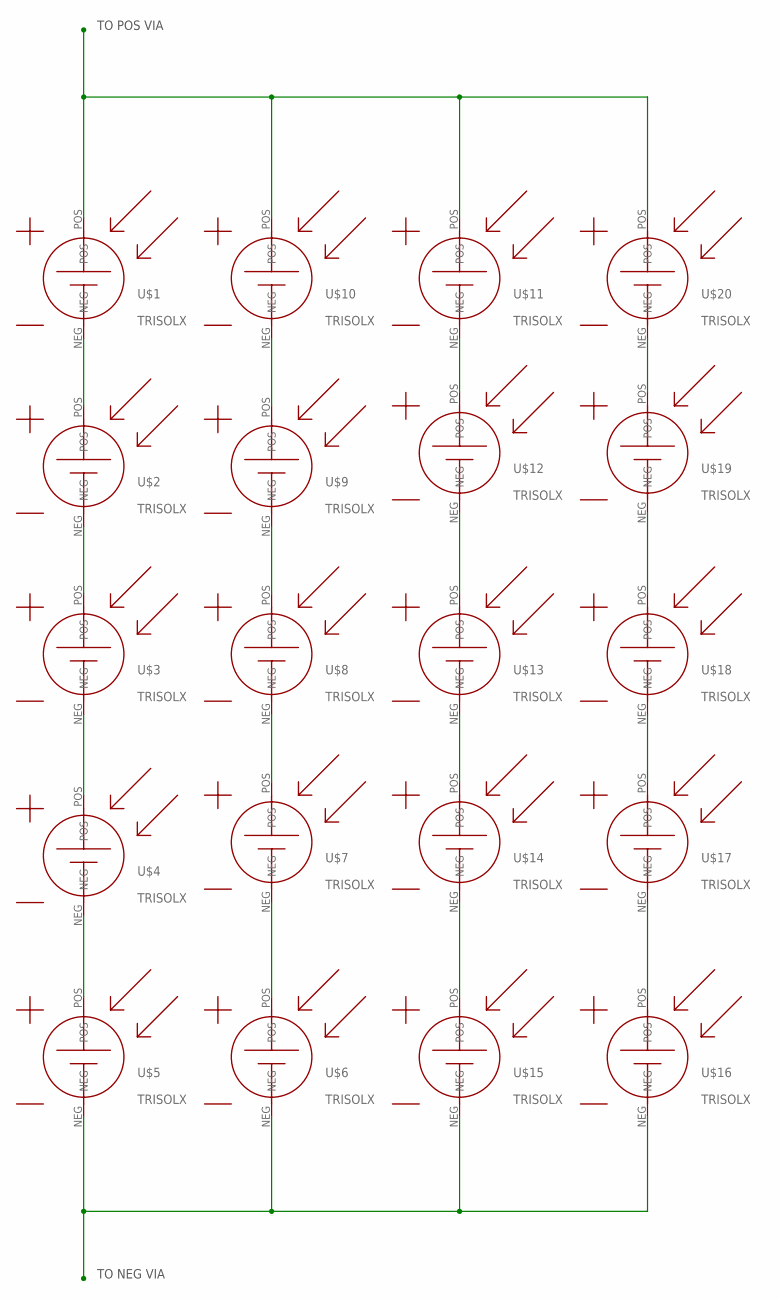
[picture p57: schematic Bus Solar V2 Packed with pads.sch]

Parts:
U$1, U$2, U$3, U$4, U$5, U$6, U$7, U$8, U$9, U$10, U$11, U$12, U$13, U$14, U$15, U$16, U$17, U$18, U$19, U$20: TRISOLX

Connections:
unnamed: U$1.NEG, U$2.POS
unnamed: U$2.NEG, U$3.POS
unnamed: U$3.NEG, U$4.POS
unnamed: U$4.NEG, U$5.POS
unnamed: U$9.POS, U$10.NEG
unnamed: U$8.POS, U$9.NEG
unnamed: U$7.POS, U$8.NEG
unnamed: U$6.POS, U$7.NEG
unnamed: U$14.NEG, U$15.POS
unnamed: U$13.NEG, U$14.POS
unnamed: U$12.NEG, U$13.POS
unnamed: U$11.NEG, U$12.POS
unnamed: U$19.POS, U$20.NEG
unnamed: U$18.POS, U$19.NEG
unnamed: U$17.POS, U$18.NEG
unnamed: U$16.POS, U$17.NEG
NEG: U$5.NEG, U$6.NEG, U$15.NEG, U$16.NEG
POS: U$1.POS, U$10.POS, U$11.POS, U$20.POS

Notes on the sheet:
TO POS VIA
TO NEG VIA

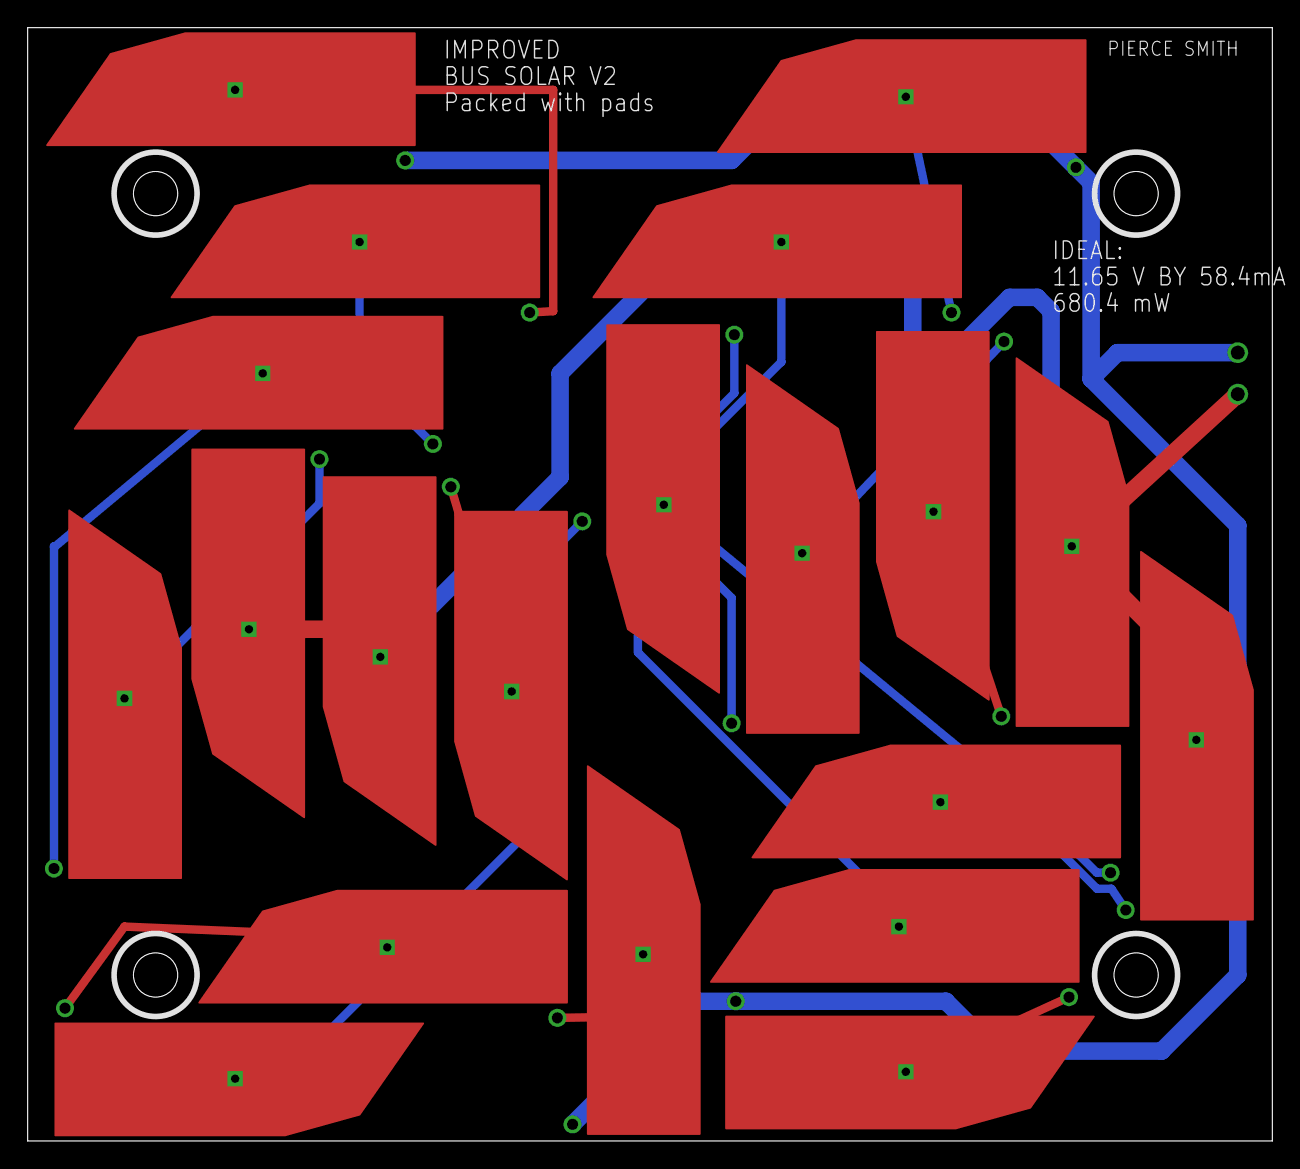
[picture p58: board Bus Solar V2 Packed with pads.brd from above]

Board: 2 copper layers, 90.0 x 80.5 mm, 20 parts (0 on the bottom side), 18 nets.

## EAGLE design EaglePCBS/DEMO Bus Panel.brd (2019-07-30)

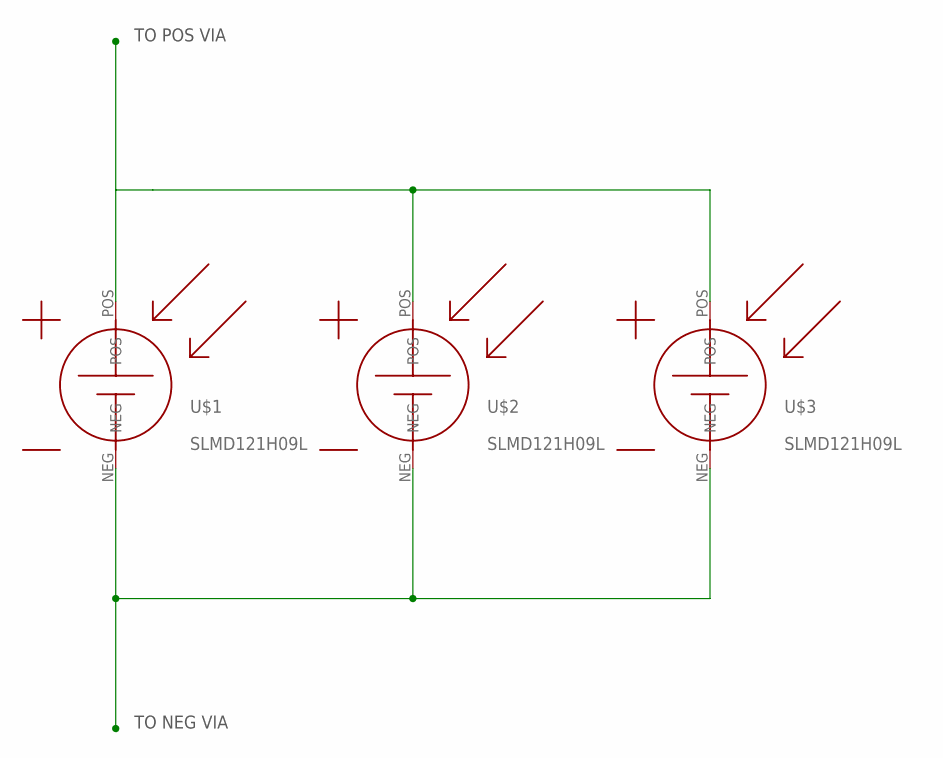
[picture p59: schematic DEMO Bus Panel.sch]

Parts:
U$1, U$2, U$3: SLMD121H09L; MONO_SOLAR_CELL_62X21

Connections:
NEG: U$1.NEG, U$2.NEG, U$3.NEG
POS: U$1.POS, U$2.POS, U$3.POS

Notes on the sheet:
TO POS VIA
TO NEG VIA

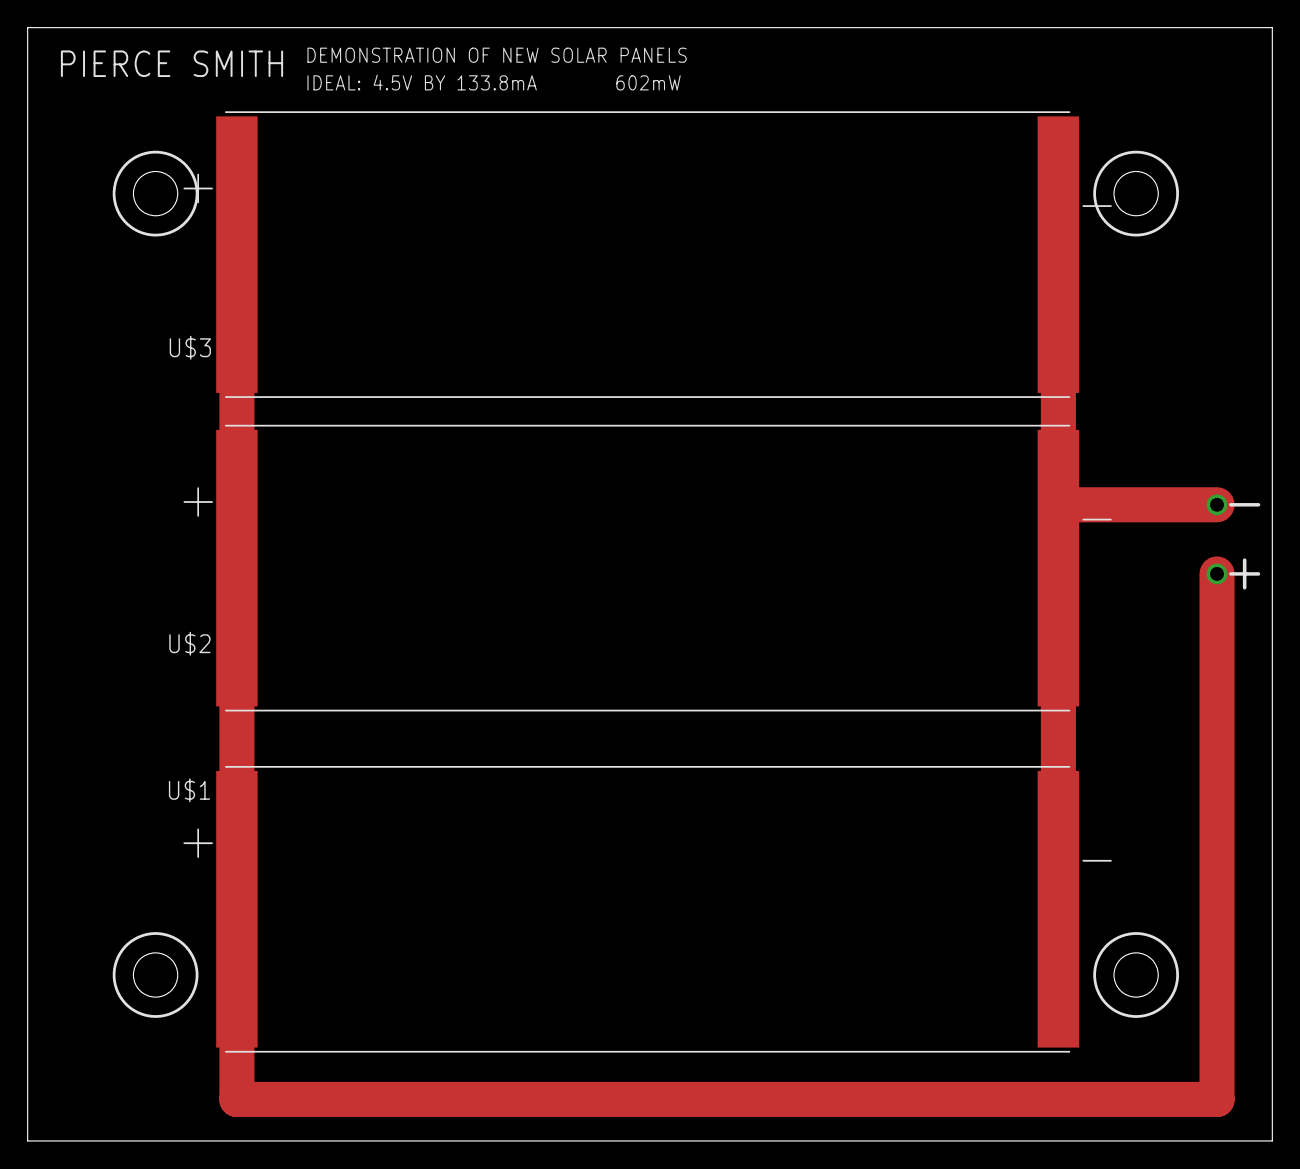
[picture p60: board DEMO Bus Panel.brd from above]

Board: 2 copper layers, 90.0 x 80.5 mm, 3 parts (0 on the bottom side), 2 nets.

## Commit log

2019-07-30 Delete 3U Payload Vibe Clamp Fixture Rev 1.pdf
    moved to Cactus-1 folder.
2019-07-30 Delete CACTUS-1 PCBs - Sensor, Pi, Solar - Autodesk Eagle.zip
    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
2019-07-30 Delete CACTUS1 Power Board Schematic.pdf
    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
2019-07-30 Delete battery specs NCR18650B.pdf
    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
